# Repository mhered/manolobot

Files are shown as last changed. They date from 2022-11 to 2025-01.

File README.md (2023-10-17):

# README - manolobot

This repo contains my notes documenting the build of my own ROS2-based mobile robot with camera and LIDAR.

This project is inspired in the phenomenal series of blog and video tutorials [Articulated Robotics](https://articulatedrobotics.xyz/) by Josh Newans.

* [Part 1](./Part-1-Getting-ready-ROS2-Aug22-Jan23.md): Notes on Articulated Robotics - Getting ready for ROS series 
* [Part 2](./Part-2-Mobile-Robot-project.md): Notes on Articulated Robotics - Making a Mobile Robot series
* [Part 3](Part-3-manolobot-Nov22.md): Notes on building **manolobot** my own ROS2-based mobile robot with camera and LIDAR
* [Part 4](Part-4-Simulation-Jan23.md): Notes on simulating the robot **manolobot_uno**
* [Part 5](Part-5-Teleoperation-Feb23.md): Notes on teleoperation for **manolobot_uno**

Go straight for the [Quick Start Guide](Quick-start-guide.md) to launch the robot and play with it

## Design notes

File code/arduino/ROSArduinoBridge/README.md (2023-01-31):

# Arduino Motor Controller

Note: Originally downloaded from https://github.com/joshnewans/ros_arduino_bridge.git
Removed .git folder to disconnect it from the original repo

This code turns an Arduino into a motor controller!
It provides a simple serial interface to communicate with a high-level computer (e.g. running ROS), and generates the appropriate PWM signals for a motor driver, to drive two motors.

This is a fork of the original code, with some changes, and removal of the ROS nodes (see [this repo](https://github.com/joshnewans/serial_motor_demo) for an alternative). Check out `README-orig.md` for the original README.

As I only have need for a subset of the functionality, I have no idea what does and doesn't work, beyond what is detailed below.
Feedback/improvements are welcome (though no promises on how quickly I'll respond). I currently only use the L298N driver, and the Arduino encoder mode.

TODO
- Finish this README

## Functionality

The main functionality provided is to receive motor speed requests over a serial connection, and provide encoder feedback.
The original code has provisions for other features - e.g. read/write of digital/analog pins, servo control, but I've never used them.

The main commands to know are

- `e` - Motor responds with current encoder counts for each motor
- `r` - Reset encoder values
- `o <PWM1> <PWM2>` - Set the raw PWM speed of each motor (-255 to 255)
- `m <Spd1> <Spd2>` - Set the closed-loop speed of each motor in *counts per loop* (Default loop rate is 30, so `(counts per sec)/30`
- `p <Kp> <Kd> <Ki> <Ko>` - Update the PID parameters

## Gotchas

Some quick things to note

- There is an auto timeout (default 2s) so you need to keep sending commands for it to keep moving
- PID parameter order is PDI (?)
- Motor speed is in counts per loop
- Default baud rate 57600
- Needs carriage return (CR)
- Make sure serial is enabled (user in dialout group)
- Check out the original readme for more

## TODO (maybe)
- Document PID tuning
- Make the speed input counts per second
- Add/test more driver boards
- Add/test other functionality

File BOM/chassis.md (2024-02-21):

# Chassis

* 290 x 190 x 124 mm Keeeper Hubert + Hilda plastic storage box with tray:  [Amazon](https://www.amazon.de/keeeper-Hubert-Hilda-Storage-Transparent/dp/B092JKYLW5?ref_=ast_sto_dp)
* Caster ball [Amazon](https://www.amazon.es/dp/B09MLVQWL7?_encoding=UTF8&psc=1&ref_=cm_sw_r_cp_ud_dp_PQB2K3KK5H9V853M14GN). Ball diameter 0.6" (16mm)

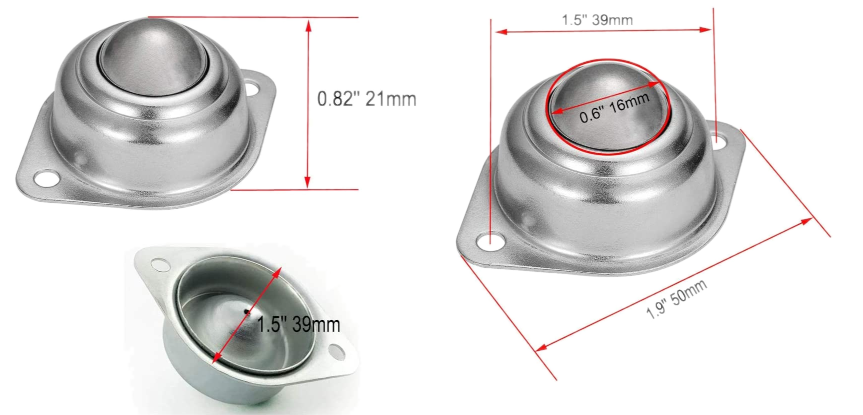
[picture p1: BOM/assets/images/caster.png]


* 2 sets of brass spacers M2.5 2: 20mm and 11mm
* Aluminium profile L shaped 30mm x 17mm x 2mm thickness, cut to 2000mm length
* M3 bolts, washers & nuts

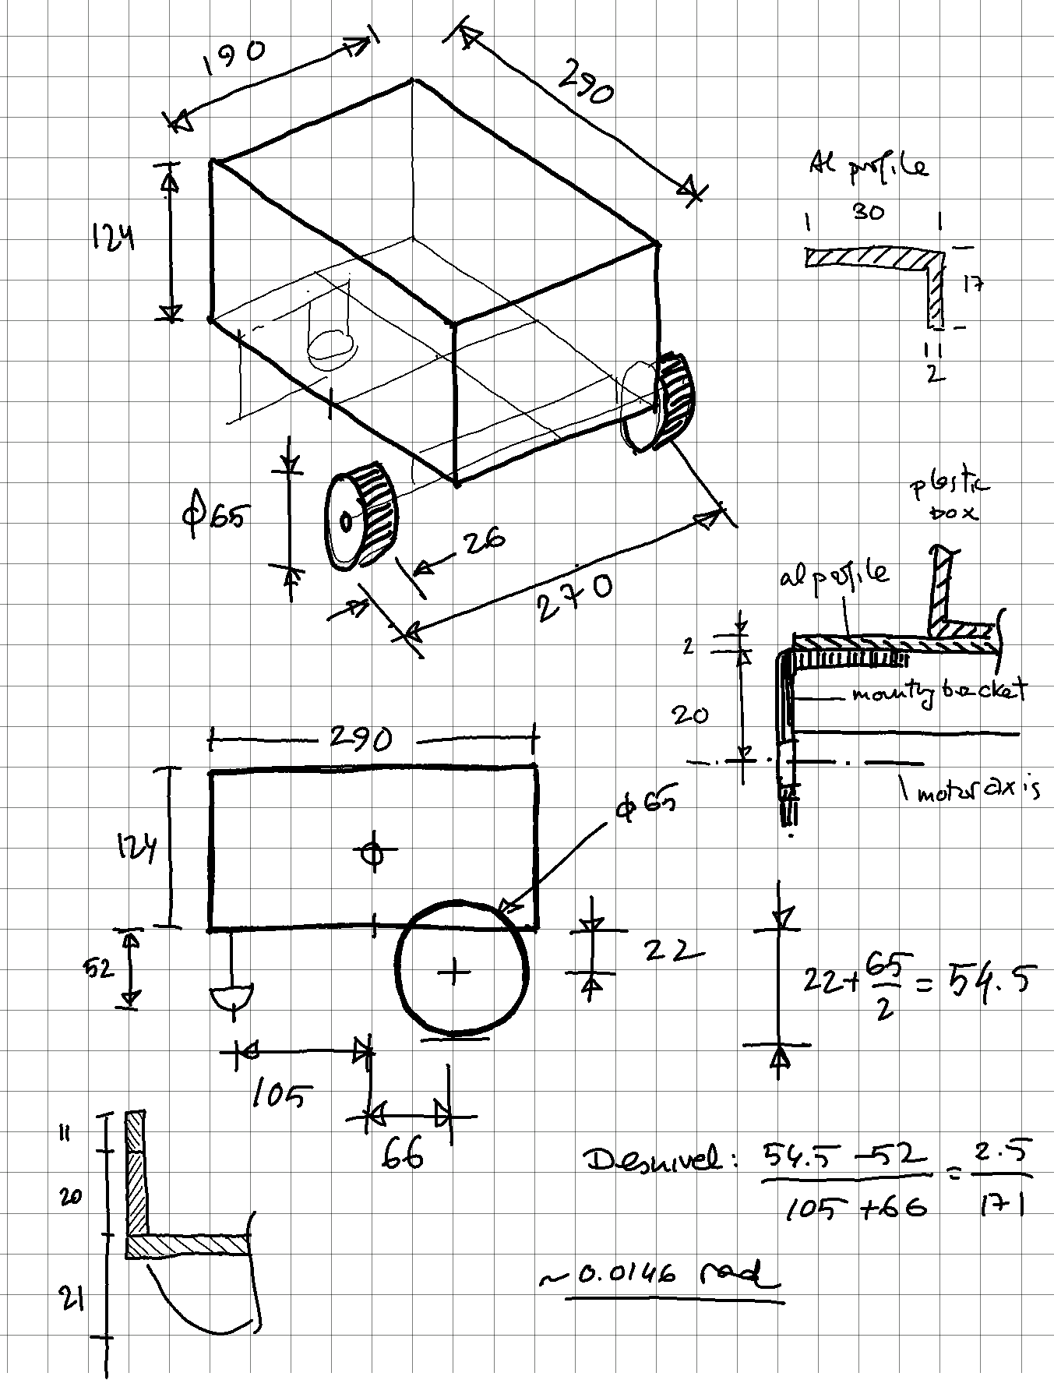
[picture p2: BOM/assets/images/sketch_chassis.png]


## 3D printed parts
### LD06 mount
* [Minipupper Oak-D-Lite & Lidar mount](https://www.thingiverse.com/thing:5374323)
* [LDRobot LD06 360 LiDAR Module & Raspberry PI Mounting Bracket](https://grabcad.com/library/ldrobot-ld06-360-lidar-module-raspberry-pi-mounting-bracket-1)
* [The original LD06 baseplate from my minipupper repo](https://github.com/mhered/minipupper_fun/tree/main/assets/CAD)

### Pi camera mount
* [BEST Micro Apex GO PRO Mount](https://www.thingiverse.com/thing:4890862)
* [Case Raspberry Pi Camera V2 (universal mounting) and GoPro holder adapter](https://www.thingiverse.com/thing:3610624)
* [Pi Camera Mount](https://www.thingiverse.com/thing:3411450)

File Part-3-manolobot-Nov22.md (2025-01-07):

# manolobot

## Bill of Materials

| Qty. | Item | Image | Description | Link | Price |
| ---- | --- | --- | --- | --- | --- |
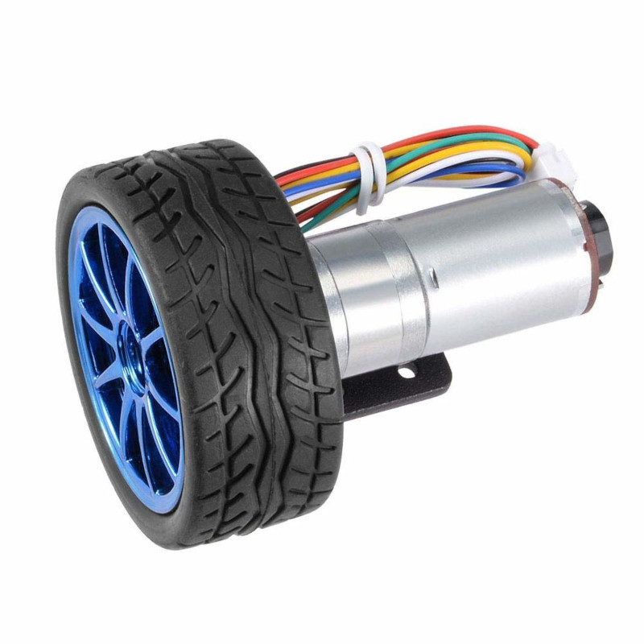
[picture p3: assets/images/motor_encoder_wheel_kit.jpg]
motor_encoder_wheel_kit
| 2 | [12V DC  encoder motor kit](./BOM/motor_kit.md) |  | 12V DC motor JGA25-371 with encoder, 130rpm reductor, 65mm wheel, coupling, mounting bracket | [Amazon](https://www.amazon.es/dp/B07WT22RNK?psc=1&ref=ppx_pop_dt_b_asin_title) | 30,33€ |
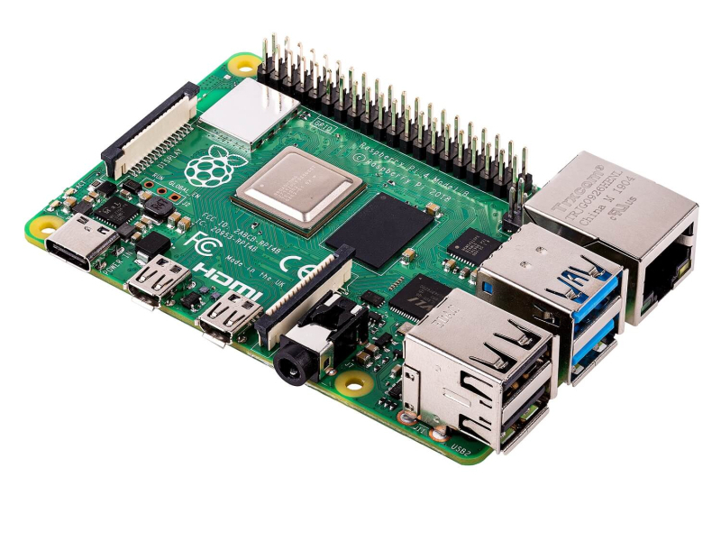
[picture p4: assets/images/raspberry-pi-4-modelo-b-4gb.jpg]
raspberry-pi-4-modelo-b-4gb
| 1 | [Raspberry Pi 4B](./BOM/RPi_4B.md) |  | | [Amazon]() | |
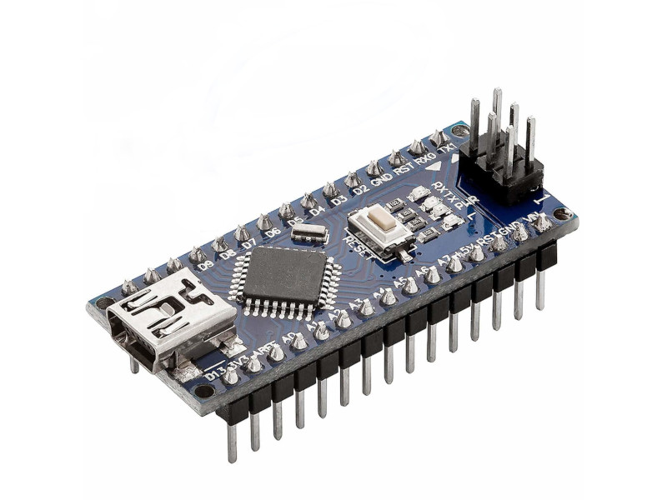
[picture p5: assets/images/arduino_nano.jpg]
arduino_nano
| 1 | [Arduino Nano V3](./BOM/arduino_nano.md) |  | AZDelivery Nano V3.0 with ATmega328 Chip CH340 soldered version with USB cable (Arduino Nano V3 clone) | [Amazon](https://www.amazon.es/gp/product/B01MS7DUEM/ref=ppx_yo_dt_b_asin_title_o00_s00?ie=UTF8&th=1) | 18,99€ |
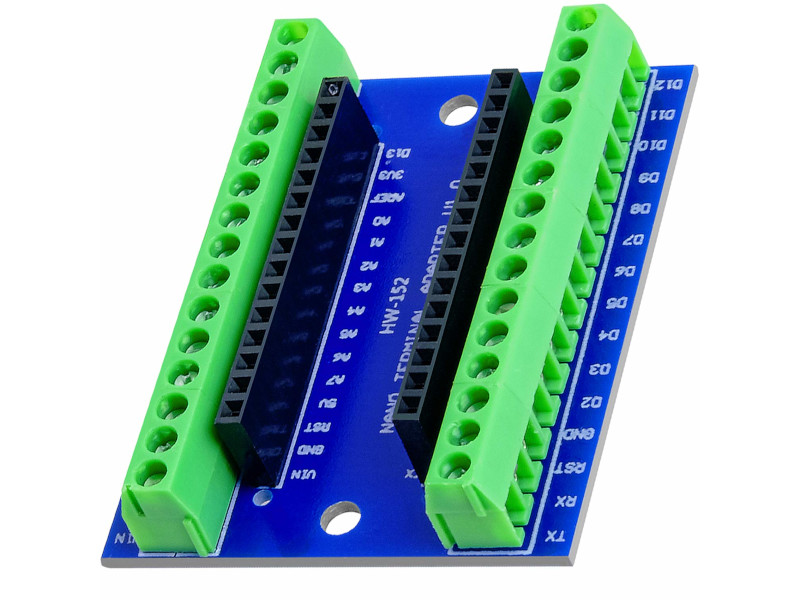
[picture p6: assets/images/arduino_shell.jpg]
arduino_shell
| 1 | Arduino Nano Shell |  | | [Amazon](https://www.amazon.es/gp/product/B08T1ZXS7K/ref=ppx_yo_dt_b_asin_title_o00_s01?ie=UTF8&th=1) | 6,99€ |
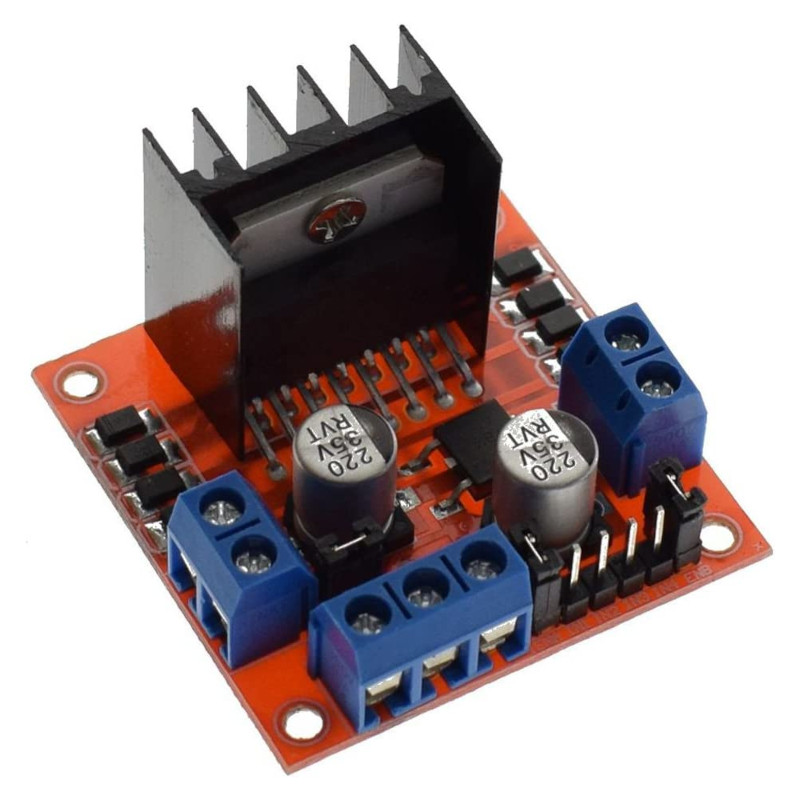
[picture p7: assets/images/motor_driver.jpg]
motor_driver
| 1 | [L298N Motor driver](./BOM/motor_driver.md) |  | | [Amazon](https://www.amazon.es/gp/product/B077NY9RY6/ref=ppx_yo_dt_b_asin_title_o00_s01?ie=UTF8&psc=1) | 9,99€ (2 uds) |
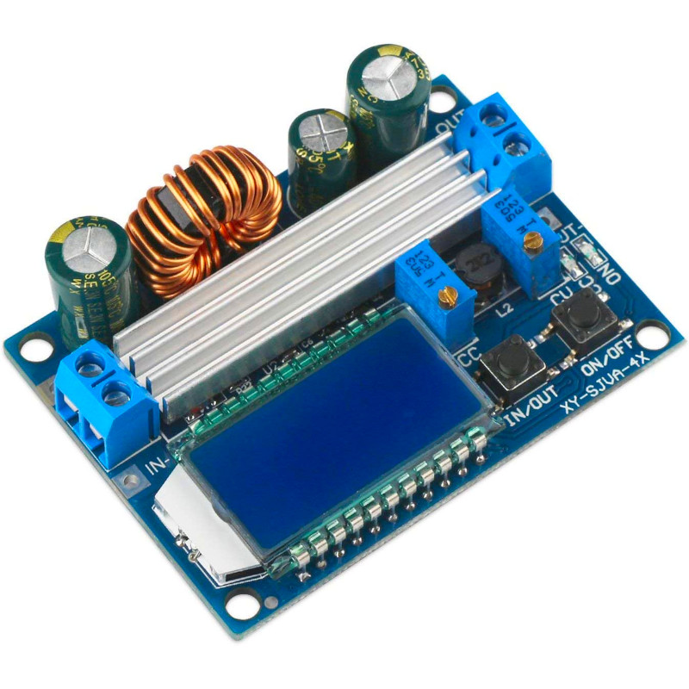
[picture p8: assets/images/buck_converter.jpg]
buck_converter
| 1 | [35W Buck-Boost DC Converter](./BOM/buck_converter.md) |  | ARCELI Buck-Boost Converter with display, DC 5.5-30V 12v to DC 0.5-30V  35W | [Amazon](https://www.amazon.es/gp/product/B07MY399GQ/ref=ppx_yo_dt_b_asin_title_o02_s00?ie=UTF8&psc=1) | 12,99€ |
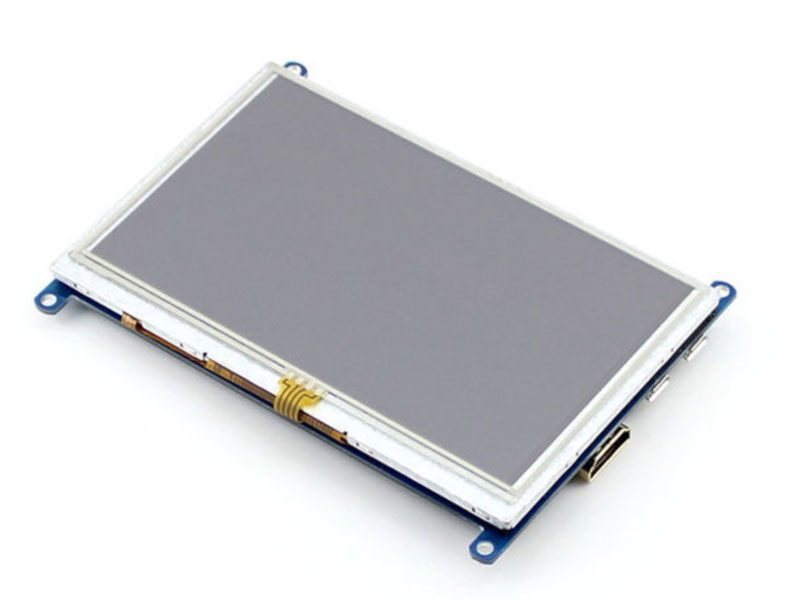
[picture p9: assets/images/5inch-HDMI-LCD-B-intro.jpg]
touchscreen
| 1 | [5" 800x480 Resistive  Touchscreen](./BOM/touchscreen.md) |  | Waveshare 5" HDMI LCD 800x480 Resistive Touchscreen TFT Display  with Case for Raspberry Pi 4 | [Amazon](https://www.amazon.es/dp/B07PLF8V8Y?psc=1&ref=ppx_pop_dt_b_product_details) | 52,99€ |
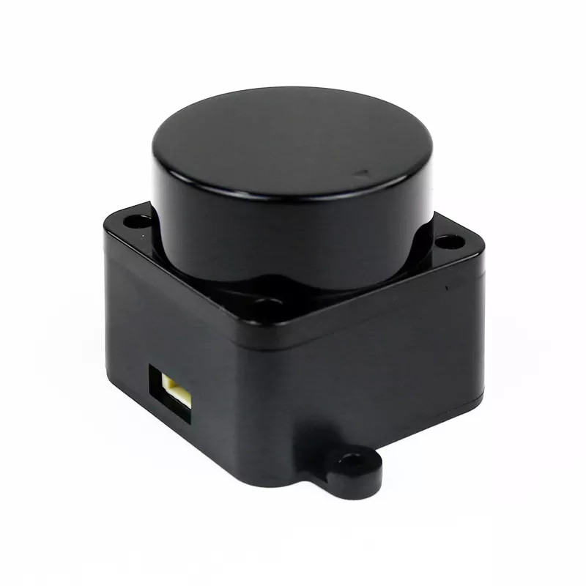
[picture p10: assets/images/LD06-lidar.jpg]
LD06-lidar
| 1 | [DTOF Lidar LD06](./BOM/LD06-lidar.md) |  | LD06 Lidar, came bundled with Minipupper | [Amazon](https://www.amazon.es/innomaker-integrado-omnidireccional-resistencia-LiDAR_LD06/dp/B08GJJX41D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) | 99,99€ |
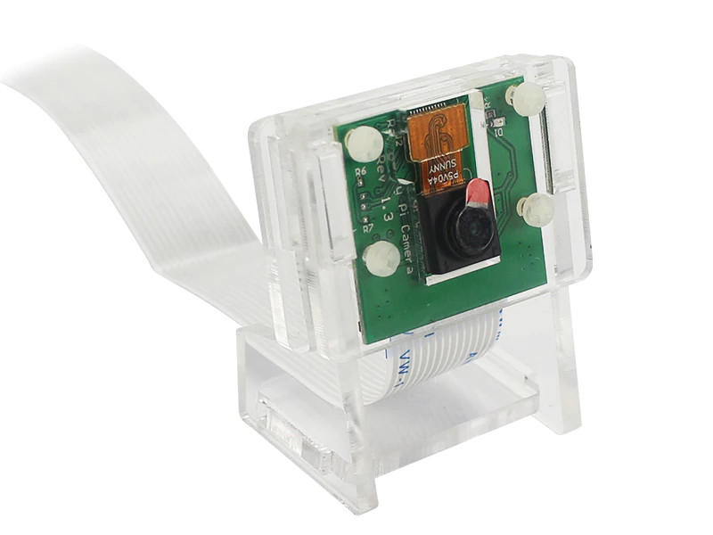
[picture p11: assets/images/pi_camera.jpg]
pi_camera
| 1 | [Pi Camera](./BOM/pi_camera.md) |  | Pi Camera v1.3 with acrilic support | | |
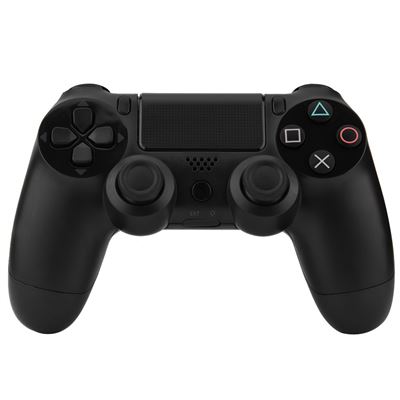
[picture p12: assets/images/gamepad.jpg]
| 1 | [Gamepad](./BOM/gamepad.md) |  | PS4-compatible Bluetooth game controller. Mine came bundled with Minipupper | [Fnac](https://www.fnac.es/mp8198387/Mando-USB-con-cable-Smart-Gamepad-para-PC-PS4/w-4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) | 17,90€ |
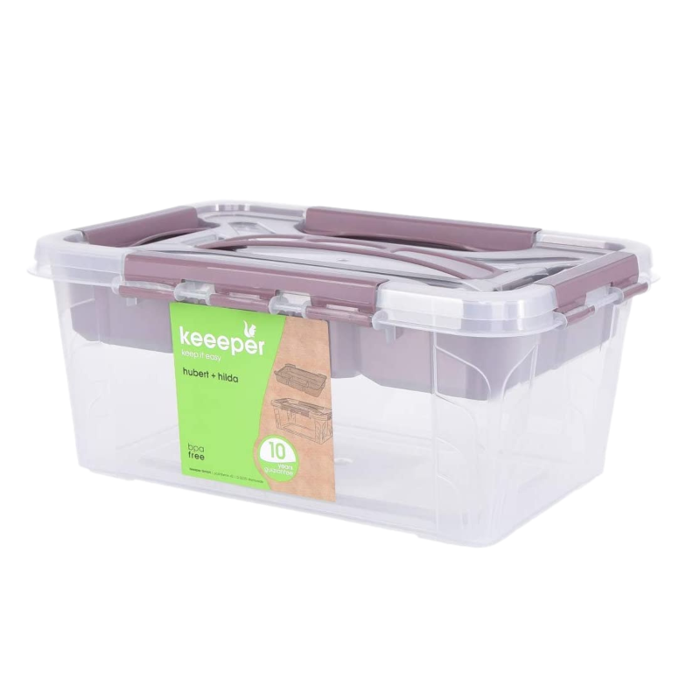
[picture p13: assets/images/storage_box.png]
| 1 | [Chassis](./BOM/chassis.md) |  | Based on a 29 x 19 x 12.4 cm Keeeper Hubert + Hilda plastic storage box with tray, used for the chassis of the robot. I purchased mine in the local Leroy Merlin. | [Amazon](https://www.amazon.de/keeeper-Hubert-Hilda-Storage-Transparent/dp/B092JKYLW5?ref_=ast_sto_dp) | 8,63€ |
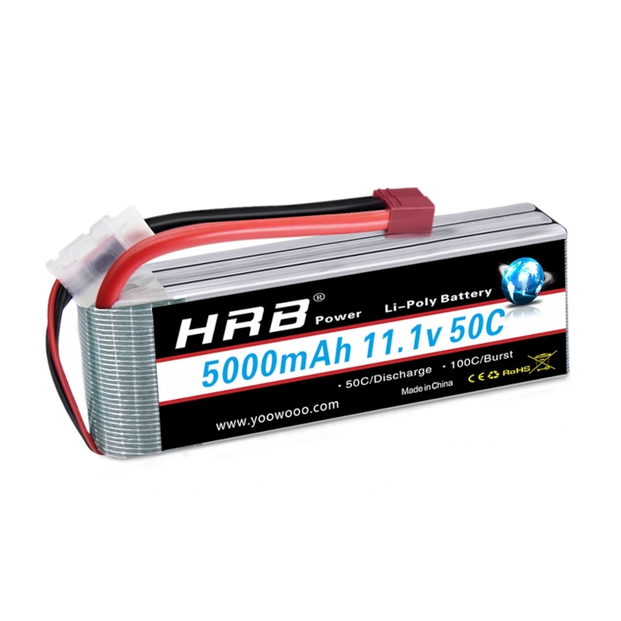
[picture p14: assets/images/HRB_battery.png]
| 1 | [Battery](./BOM/battery.md) |  | HRB Battery RC LiPo 5000mAh 11.1V 3S 50C XT60 Connector with 4 adapter parts. 308 g. | [Amazon](https://www.amazon.es/gp/product/B086JP7PCC/) | 35,99€ |
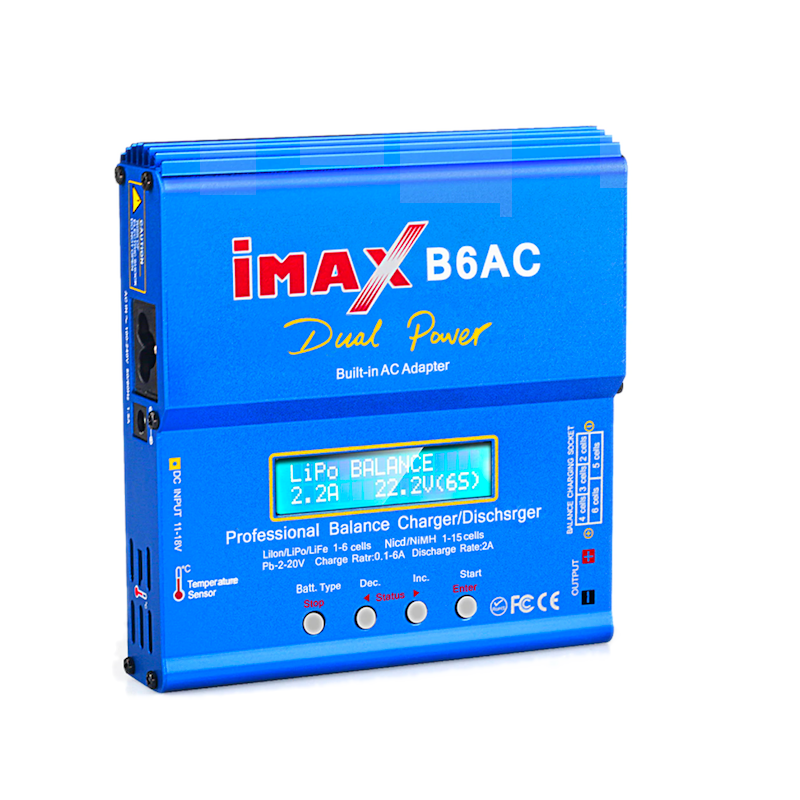
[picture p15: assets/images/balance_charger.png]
| 1 | Balance charger |  | WANGCL IMAX B6AC Lipo Battery charger B6 80W Digital LCD Lipo Cargador  11-18V con adaptador para plomo ácido NI-CD/NI-MH 1-6S LI-PO | [Amazon](https://www.amazon.es/gp/product/B0B3GM8KX9/) | 42,99€ |
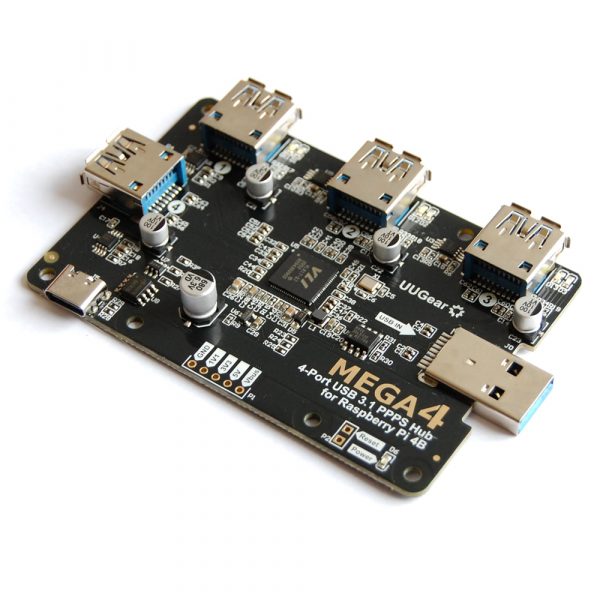
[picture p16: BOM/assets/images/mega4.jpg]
| 1 | [Mega4 USB Hub](./BOM/mega4.md) |  | UUGEAR MEGA4: 4-Port USB 3.1 PPPS Hub for Raspberry Pi 4B | [The Pi Hut](https://thepihut.com/products/mega4-4-port-usb-3-1-ppps-hub-for-raspberry-pi-4) | £29,00 |

## First prototype (20/11/22)

- 12V from bench power source
- A split takes the 12V to the buck converter and the motor driver.
- Buck converter takes 12V at IN+ /IN- and yields 5V at OUT+/OUT- to power the RPi
- RPi takes 5V at pin 4 (5V)/ pin 6(GND) - [How do I power my Raspberry Pi](https://robocraze.com/blogs/post/how-do-i-power-my-raspberry-pi)
- Arduino Nano powered from RPi via USB
- Motor Driver is powered by 12V at 12V/GND pins. 5V jumper is installed, 5V terminal not connected - Could I use this to power the RPi?
- OUT1/OUT2 are connected to the Red/White of the motor. The remaining 4 cables of the encoder are disconnected.
- Connecting the IN1 / IN2 to 5V (e.g. to the 5V pin of the Arduino Nano, cfr. [the Nano pinout in this tutorial](https://diyi0t.com/arduino-nano-tutorial/)) makes the Motor rotate CV / CCV  

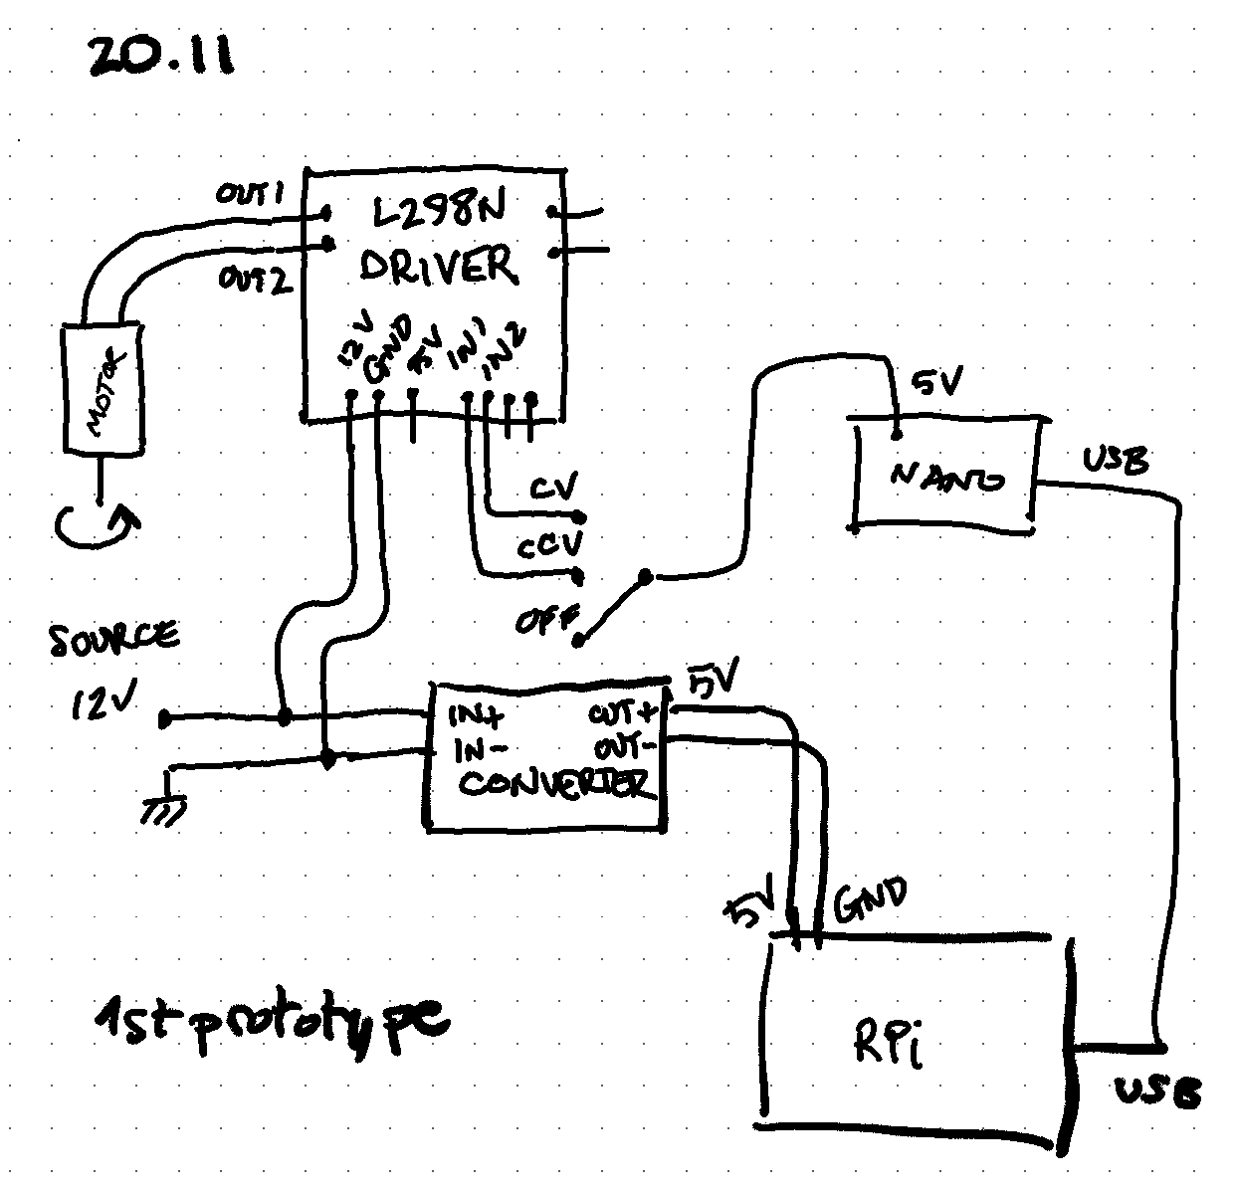
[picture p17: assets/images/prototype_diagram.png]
prototype_diagram


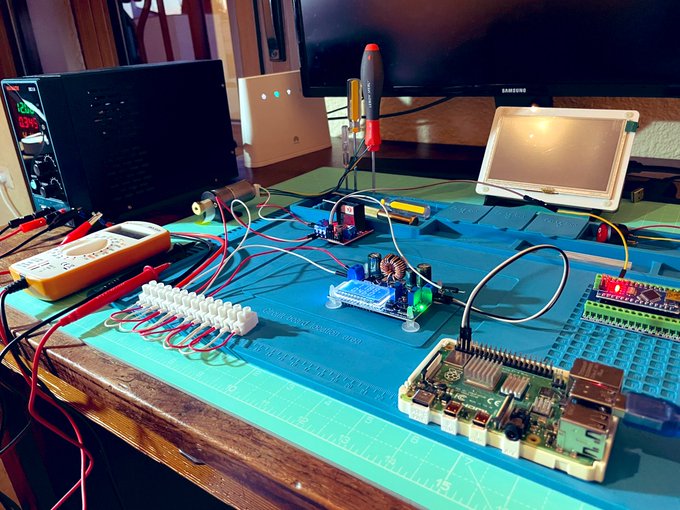
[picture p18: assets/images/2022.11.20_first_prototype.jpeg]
first_prototype


### Shutting down

Before switching off the power supply, SSH into the RPi to shut it down:

```bash
(RPi) $ sudo shutdown -h now
```

Note: Powering the adafruit USB hub https://forums.adafruit.com/viewtopic.php?p=930206&hilit=external+power+usb+hub#p930206

## Prototype status (4/12/22)

- installed fuse and switch
- replaced split with AWG22 cable
- installed second motor
- connected Pi camera, LD06 lidar and LCD screen
- made a USB-C pigtail to connect RPi (powering from pins cannot run accesories)
- ordered spacers, USB-C pigtails, a flat HDMI cable and a USB hub

## Prototype status (28/12/22)

* installed flat HDMI cable, USB-C pigtail
* discarded USB hub (not needed)

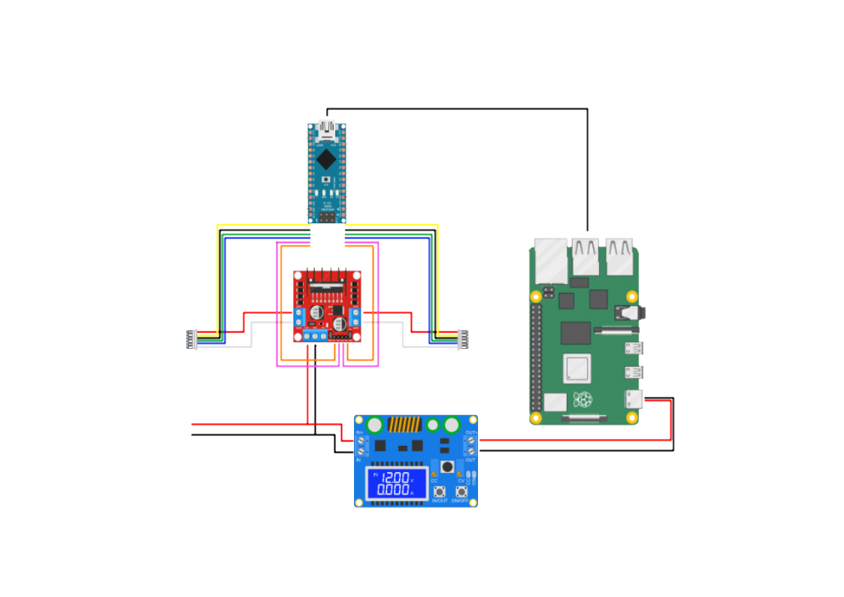
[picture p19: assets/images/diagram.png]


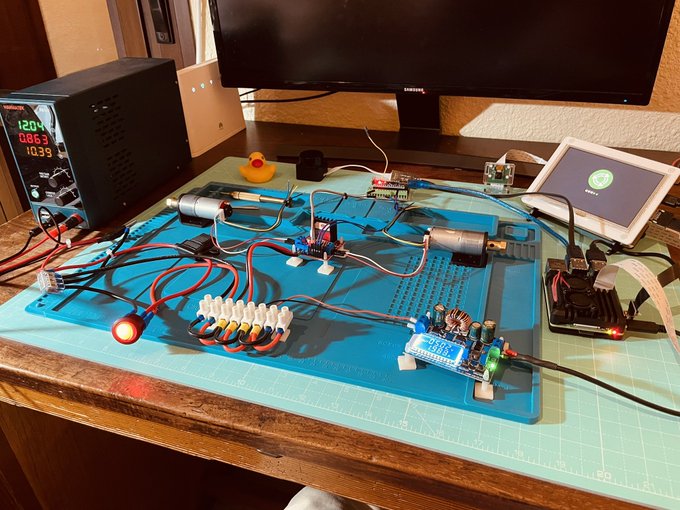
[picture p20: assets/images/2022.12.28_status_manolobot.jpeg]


## Controlling the motors with a joystick (4/1/23)

Code: [./code/arduino/motor_joystick/motor_joystick.ino](./code/arduino/motor_joystick/motor_joystick.ino) 

The script was originally inspired on [this example code for the joystick](https://www.luisllamas.es/arduino-joystick/) and [this script for controlling motors](https://lastminuteengineers.com/l298n-dc-stepper-driver-arduino-tutorial/), and later refined with [this implementation](https://howtomechatronics.com/tutorials/arduino/arduino-dc-motor-control-tutorial-l298n-pwm-h-bridge/) (using [Arduino's map() function](https://www.arduino.cc/reference/en/language/functions/math/map/) ) and [this discussion on translating joystick positions to motor speeds](https://coderdojoathenry.org/2019/02/24/hackers-how-to-control-a-robots-wheel-motors-based-on-joystick-movements/).

Notes:

* For motors A and B connect only motor voltage (WHITE, RED) to the motor driver L298N, keeping encoder disconnected (BLUE,GREEN, BLACK,YELLOW)
* In the motor driver L298N, remove the brakers in ENA and ENB 
* Connect as per following table and diagram:

| Description | Component pin | Arduino pin |
| --- | ---- | ---- |
| Motor A speed (analog) | ENA  | D9 |
| Motor A direction | IN1 | D8 |
| Motor A direction | IN2 | D7 |
| Motor B speed (analog) | ENB | D3 |
| Motor B direction | IN3 | D5 |
| Motor B direction | IN4 | D4 |
| Joystick: command rotation (analog) | VRX | A0 |
| Joystick: command forward / backward motion (analog) | VRY | A1 |

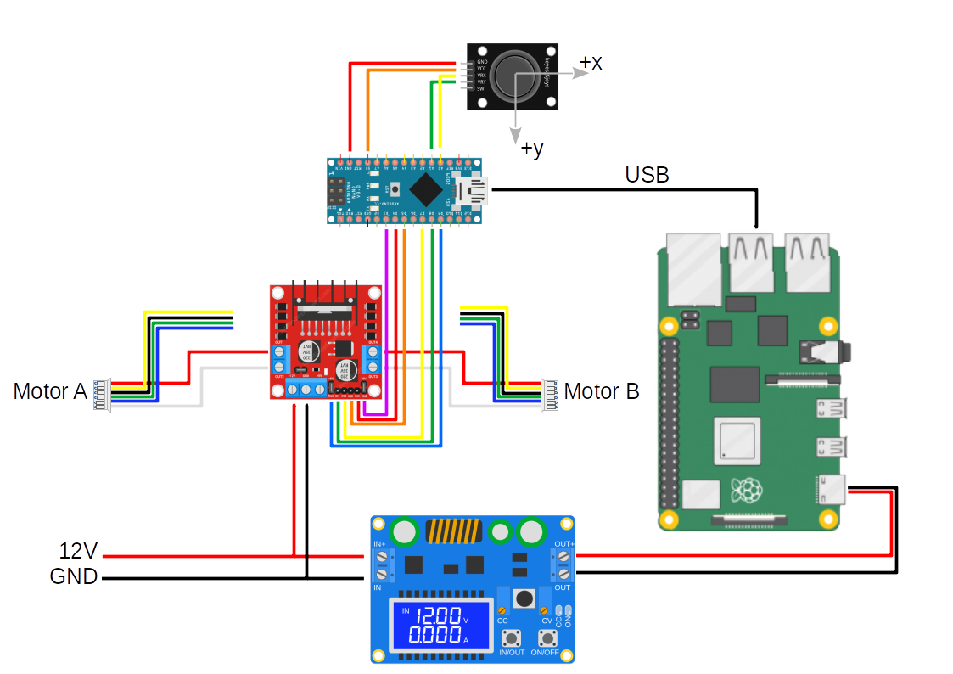
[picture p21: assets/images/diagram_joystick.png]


* Analog output of VRX, VRY is in the range 0 - 1023. 
* Analog input of ENA and ENB in the range 0-255. 
* To change direction of rotation of Motor A reverse input to IN1 - IN2  from HIGH - LOW to LOW - HIGH
* Idem for Motor B, IN3, IN4

The script allows to control the motors with the joystick. Moving the stick in the Y direction turns both wheels forward / backward. Moving the stick in X direction moves the wheels in opposite directions to make the robot turn. The script also prints output through serial. 

## `miniterm` to monitor serial in the Arduino from the laptop (and through the RPi)

1. install `miniterm` in PC and RPi

```bash
$ sudo apt install python3-serial
```

2. add the user to the dialout group:

```bash
$ sudo adduser mhered dialout
```

3. usage:

```bash
$ miniterm

--- Available ports:
---  1: /dev/ttyAMA0         'ttyAMA0'
---  2: /dev/ttyUSB0         'USB2.0-Ser!'
--- Enter port index or full name: 2
--- Miniterm on /dev/ttyUSB0  9600,8,N,1 ---
--- Quit: Ctrl+] | Menu: Ctrl+T | Help: Ctrl+T followed by Ctrl+H ---
(X, Y): (508, 517) | motorA: 0% | motorB: 1%
(X, Y): (510, 517) | motorA: 0% | motorB: 1%
(X, Y): (510, 517) | motorA: 0% | motorB: 1%
(X, Y): (510, 516) | motorA: 0% | motorB: 1%
(X, Y): (510, 22) | motorA: -96% | motorB: -95%
(X, Y): (493, 0) | motorA: -100% | motorB: -96%
(X, Y): (510, 517) | motorA: 0% | motorB: 1%
(X, Y): (510, 1023) | motorA: 99% | motorB: 100%
(X, Y): (510, 1022) | motorA: 99% | motorB: 100%
(X, Y): (1023, 1023) | motorA: 100% | motorB: 0%
(X, Y): (1023, 850) | motorA: 100% | motorB: -34%
(X, Y): (1023, 517) | motorA: 100% | motorB: -99%
(X, Y): (661, 517) | motorA: 29% | motorB: -28%
(X, Y): (0, 517) | motorA: -99% | motorB: 100%
(X, Y): (0, 517) | motorA: -99% | motorB: 100%
...
```

Note: to stop `miniterm` with a Spanish keyboard press  `Ctrl + Alt Gr + ]` 

## VS Code Remote and Arduino extensions

Check out this video on how to write and upload to arduino from the laptop and through the RPi: https://www.youtube.com/watch?v=2BJ-iJF04VA

Highlights of the installation:

* Copy & Paste **only** the path of the folder where the `arduino` executable is, e.g. in the case below paste only `/home/mhered/Applications/arduino-1.8.19/`:

`````bash
$ ls -l `which arduino`
lrwxrwxrwx 1 root root 48 Sep  9 02:02 /usr/local/bin/arduino -> /home/mhered/Applications/arduino-1.8.19/arduino
`````

* No need to select a programmer, see [here](https://support.arduino.cc/hc/en-us/articles/6125080065820-Select-programmer-in-Arduino-IDE)
* Edit `.vscode/arduino.json` to add `"output":"build"` to avoid the message that it cannot use precompiled files

Highlights of the usage:

* To launch **Remote SSH** click in the green square in the bottom left corner of VS Code, select **Connect to Host** and select the host, then enter the password
* Every new session: Open the Command panel with  `Ctrl + Shift + P` then start typing "Select" for **Arduino: Select Sketch**. The file `.vscode/arduino.json` stores the selection of `port`, `sketch`, `board`, `configuration`, `output` otherwise select manually in the lower blue bar.
* To compile: command **Arduino: Verify**. Monitor progress on the OUTPUT / Arduino window. Wait for it to finish before uploading.
* To flash: command **Arduino: Upload**. Wait for compile to complete before uploading. Does not work if `miniterm` is running.
* To monitor serial: use `miniterm` in a new Terminal
* To add libraries: command **Arduino: Library Manager**

## Chassis (7/1/23)

* First test on the chassis

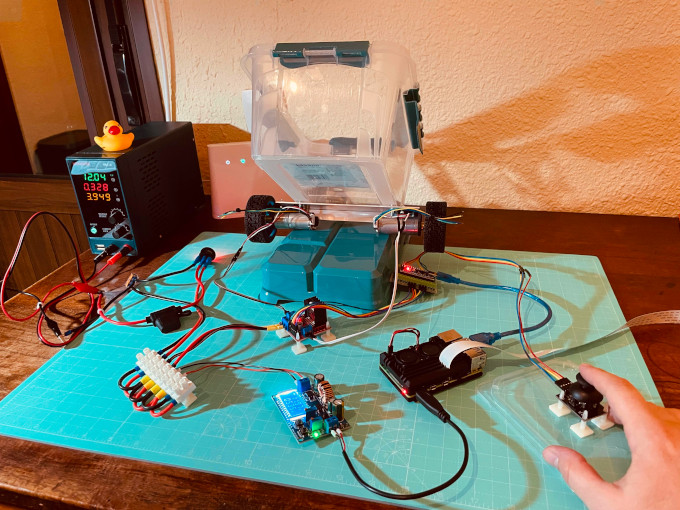
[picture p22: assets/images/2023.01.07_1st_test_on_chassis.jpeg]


* All aboard! - including the rubber duckie

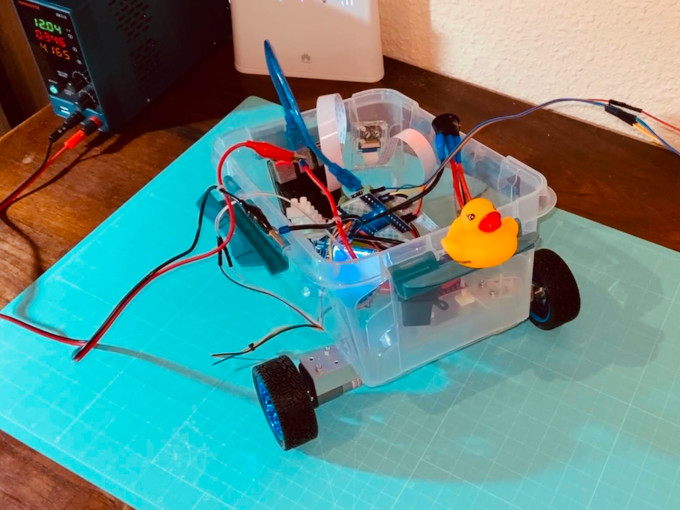
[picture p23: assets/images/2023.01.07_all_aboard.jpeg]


## Details (12/1/23)

* Adding details: casters, grommets, a switch...

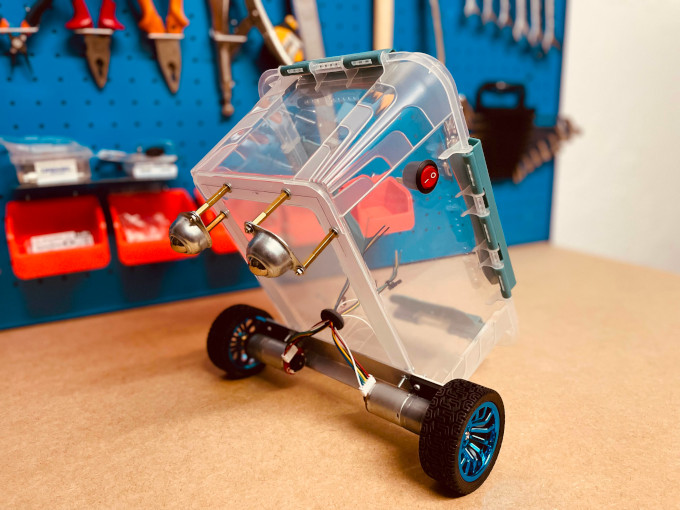
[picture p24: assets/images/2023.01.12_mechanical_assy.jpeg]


* All the electronics back in



## Order in the house (17/1/23)

* Some order inside the chassis:



## Selfie  (21/1/23)

* A selfie to celebrate that the camera onboard the `manolobot_uno ` is broadcasting!



## Prototype status (29/01/23)

* Screen, safe reset/shutdown button and 3D printed camera support







## Running motors from the PC (31.01.23)

1. Clone `ROSArduinoBridge` from https://github.com/joshnewans/ros_arduino_bridge.git to `./code/arduino/` - removed the `.git` folder to disconnect it from original repo
2. Upload software to the Arduino
3. Rewire Arduino:

| Description | From | To |
| --- | --- | --- |
| Motor A (Left) , power + (can be reversed with White to move motor forward and reverse) | Motor A (Left) , Red | L298, OUT1 |
| Motor A (Left), power - (can be reversed with Red to move motor forward and reverse) | Motor A (Left) , White | L298, OUT2 |
| Motor B (Right), power + (can be reversed with White to move motor forward and reverse) | Motor B (Right), Red | L298, OUT4 |
| Motor B (Right), power - (can be reversed with Red to move motor forward and reverse) | Motor B (Right), White | L298, OUT3 |
| Motor A (Left) direction | L298, IN1 | Arduino, D10 |
| Motor A (Left) direction | L298, IN2 | Arduino, D6 |
| Motor B (Right) direction | L298, IN3 | Arduino, D9 |
| Motor B (Right) direction | L298, IN4 | Arduino, D5 |



4. Run `miniterm` to test it (`-e` for interactive and specify the baud rate or it won't work at 9600):

```bash
(RPi):$ $ miniterm -e /dev/ttyUSB0 57600
--- Miniterm on /dev/ttyUSB0  57600,8,N,1 ---
--- Quit: Ctrl+] | Menu: Ctrl+T | Help: Ctrl+T followed by Ctrl+H ---
o 150 150
OK
o -200 200
OK
--- exit ---
```

## With encoders

Wiring:



| Description | From | To |
| --- | --- | --- |
| Motor A (Left) , power + (can be reversed with Red to move motor forward and reverse) | Motor A (Left) , Red | L298, OUT1 |
| Motor A (Left), Encoder power - (Voltage range 3.3-5V. Positive and negative can not be connected incorrectly) | Motor A (Left) , Black | Arduino, GND |
| Motor A (Left), Encoder A phase signal feedback (11 signals per turn of the motor) | Motor A (Left) , Yellow | Arduino, D3 |
| Motor A (Left), Encoder B phase signal feedback (11 signals per turn of the motor) | Motor A (Left) , Green | Arduino, D2 |
| Motor A (Left), Encoder power supply + (Voltage range 3.3-5V. Positive and negative can not be connected incorrectly) | Motor A (Left) , Blue | Arduino, 5V |
| Motor A (Left), power - (can be reversed with Red to move motor forward and reverse) | Motor A (Left) , White | L298, OUT2 |
| Motor B (Right), power + (can be reversed with Red to move motor forward and reverse) | Motor B (Right), Red | L298, OUT4 |
| Motor B (Right), Encoder power - (Voltage range 3.3-5V. Positive and negative can not be connected incorrectly) | Motor B (Right), Black | Arduino, GND |
| Motor B (Right), Encoder A phase signal feedback (11 signals per turn of the motor) | Motor B (Right), Yellow | Arduino, A4 |
| Motor B (Right), Encoder B phase signal feedback (11 signals per turn of the motor) | Motor B (Right), Green | Arduino, A5 |
| Motor B (Right), Encoder power supply + (Voltage range 3.3-5V. Positive and negative can not be connected incorrectly) | Motor B (Right), Blue | Arduino, 5V |
| Motor B (Right), power - (can be reversed with Red to move motor forward and reverse)e | Motor B (Right), White | L298, OUT3 |
| Motor A (Left) direction | L298, IN1, Green | Arduino, D10 |
| Motor A (Left) direction | L298, IN2, Yellow | Arduino, D6 |
| Motor B (Right) direction | L298, IN3, Orange | Arduino, D9 |
| Motor B (Right) direction | L298, IN4, Red | Arduino, D5 |

## Calibration

See https://www.youtube.com/watch?v=-PCuDnpgiew

`encoder_cpr` empirically estimated as 1975 encoder counts / revolution

`loop_rate` (or `PID_RATE`) is set to 30 Hz (PID loops/s)

To set a wheel speed of R rev/s we send to the closed loop a command in counts per PID loop so: 

(R rev/s) * (1975 counts/rev) /(30 PID loops/s) = R*1975/30 counts/PID loop = 66 R counts/PID loop

i.e. to rotate both wheels forward at 1 rev/s: `m 66 66`

to rotate both wheels backwards at 2 rev/s: `m -132 -132`

etc

## To do

- [x] connect motors 
- [x] install and test basic motor software
- [x] configure and test camera
- [x] configure and test lidar
- [x] purchase and install battery
- [x] soft powerdown button
- [x] USB hub
- [x] solve issues with screen
- [x] 3D printed parts
- [x] connect and test encoders
- [x] command motor through ROS 
- [x] teleoperation with gamepad
- [ ] improve layout of components inside chassis
- [ ] configure face in screen

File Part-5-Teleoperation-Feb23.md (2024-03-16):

# Teleoperation

Teleoperation is about sending command signals to the robot, and receiving sensor feedback from the robot.

Roadmap:

- Demo GUI ROS node
- `teleop_twist_keyboard` with `ros2_control`
- teleop with a gamepad
- teleop with a phone

## Demo GUI ROS node

1. In the RPi clone the repo and symlink to src, build and source:

```bash
(RPi): $ cd ~/git/ && git clone https://github.com/joshnewans/serial_motor_demo.git
(RPi): $ ln -s ~/git/serial_motor_demo/ ~/dev_ws/src/
(RPi): $ cd ~/dev_ws/
(RPi): $ colcon build --symlink-install
(RPi): $ source install/setup.bash
```

2. Run the driver node in the RPi:

```bash
(RPI):$ ros2 run serial_motor_demo driver --ros-args -p serial_port:=/dev/ttyUSB0 -p baud_rate:=57600 -p loop_rate:=30 -p encoder_cpr:=1975
Connecting to port /dev/ttyUSB0 at 57600.
Connected to Serial<id=0xffff80b8ec40, open=True>(port='/dev/ttyUSB0', baudrate=57600, bytesize=8, parity='N', stopbits=1, timeout=1.0, xonxoff=False, rtscts=False, dsrdtr=False)
Error: Serial timeout on command: e

```

3. Repeat the process in the PC and run the GUI:

```bash
(PC): $ cd ~/git/ && git clone https://github.com/joshnewans/serial_motor_demo.git
(PC): $ ln -s ~/git/serial_motor_demo/ ~/dev_ws/src/
(PC): $ colcon build --symlink-install
(PC): $ cd ~/dev_ws/
(PC): $ source install/setup.bash

(PC):$ ros2 run serial_motor_demo gui
```



## Teleop with the keyboard (`teleop_twist_keyboard` and `ros2_control`)

cfr: https://articulatedrobotics.xyz/mobile-robot-12-ros2-control/

cfr: https://control.ros.org/master/index.html

Using ROS topics is not fast enough

`ros2_control` is faster (loads libraries) and allows writing modular reusable code



### Controller manager

**Controller manager** connects hardware drivers with control algorithms using plugins

2 ways to run it:

* normally you use the one provided `controller_manager/ros2_control_node`
* you may want to write your own node of class `controller_manager::ControllerManager`

Provide info about the hardware interfaces via the URDF file and the controllers via a YAML parameters file

Interacting with the controller manager:

* via ROS services
* via `ros2_control` CLI tool that simplifies the calls to these services
* via specialized nodes and scripts

### Hardware interfaces 

**Hardware interfaces or components** are pieces of software that speak to the hardware and expose it in the standard of `ros2_control`. They represent the hardware through **Command interfaces** (read/write, things we can control in the robot, e.g. motor velocity) and **State interfaces** (read only, things we can only monitor, e.g. wheel position and velocity, battery level, temperature, etc)

A robot may have multiple hardware components. The **controller manager** uses the **resource manager** to gather all the hardware interfaces and exposes them together so the controller manager sees a long list of command and state interfaces. We include `ros2_control` tags in the URDF to list the hardware interfaces (plugins) the resource manager must load.

### Controllers

The way we interact with `ros2_control` listen for input e.g. gamepad or navigation path planner

They listen for some topic, calculate proper actuations and send command inputs to the hardware interfaces through controller manager and resource manager

Controllers are designed for specific robot applications, and are hardware independent. Many are provided in `ros2_controller` package. E.g. the `diff_drive_controller/DiffDriveController`

We set up the controllers through a YAML file that sets parameters

We can have several controllers provided they are not trying to command the same interfaces, but they can share state interfaces (read only)

Controllers do not need to actually control anything, can be used e.g. just to read a state interface and publish it to a ROS topic

### In practice (with gazebo)

1. Install packages:

```bash
(PC):$ sudo apt install ros-foxy-ros2-control ros-foxy-ros2-controllers ros-foxy-gazebo-ros2-control
```

2. update URDF file `./manolobot_uno/description/robot.urdf.xacro` to call `ros2_control.xacro` instead of `gazebo_control.xacro`
3. Create [`./manolobot_uno/description/ros2_control.xacro`](./manolobot_uno/description/ros2_control.xacro) and YAML parameter file `./manolobot_uno/config/my_controllers.yaml`
4. build and source
5. run with:

```bash
(PC):$ ros2 launch manolobot_uno launch_sim.launch.py world:=./src/manolobot_uno/worlds/cones.world
```

6. Check hardware interfaces are working with:

```bash
(PC):$ ros2 control list_hardware_interfaces
command interfaces
	left_wheel_joint/velocity [unclaimed]
	right_wheel_joint/velocity [unclaimed]
state interfaces
	 left_wheel_joint/position
	 left_wheel_joint/velocity
	 right_wheel_joint/position
	 right_wheel_joint/velocity
```

7. start controllers with the `spawner.py` script which will later on work nicely for a launch file

```bash
(PC):$ ros2 run controller_manager spawner.py diff_cont
```

8. To run `teleop_twist_keyboard` we need to remap `/cmd_vel` to  `/diff_cont/cmd_vel_unstamped` which is what the controller expects:

```bash
(PC):$ ros2 run teleop_twist_keyboard teleop_twist_keyboard --ros-args -r /cmd_vel:=/diff_cont/cmd_vel_unstamped
```

### In practice (fixing details)

cfr: https://articulatedrobotics.xyz/mobile-robot-12a-ros2-control-extra/

#### Increase gazebo clock rate

Robot movement is choppy because clock rate in Gazebo is too slow (10Hz). Increased to 400Hz because why not.

**Note:** After implementing the fix to increase gazebo clock rate, I get the following error message when running gazebo - even though it otherwise  seems to be working fine:

```
...
[gzserver-2] Error [parser.cc:403] Error parsing XML in file [/home/mhered/dev_ws/install/manolobot_uno/share/manolobot_uno/config/gazebo_params.yaml]: Error document empty.
...
```

If appears it is trying to interpret the `gazebo_params.yaml` file as XML and failing.

#### Reduce wheel drift

Replace wheel collision model for spheres

#### Add parameter to toggle between `gazebo_control` and `ros2_control`

Because `ros2_control` shows misbehavior at higher speeds (?)

- [x] To Do: add toggle at runtime, i.e. `$ ros2 launch my_package launch_sim.launch.py use_ros2_control:=false`

### In practice (in the actual robot)

cfr: https://articulatedrobotics.xyz/mobile-robot-13-ros2-control-real/

We want to link the command velocity (`Twist` or `TwistStamped` messages from a gamepad or Nav2 or whatever) with the actual motors in the robot.

In our case:

* we use the `diff_drive_controller` controller plugin to convert command velocities into required wheel velocities. 
* we need to write a hardware interface plugin or clone `diffdrive_arduino` by Josh Newans - this converts required wheel velocities into motor hardware commands
* The controller manager (`ros2_control_node`) links the two plugins.
* Joint State Broadcaster reads wheel encoder positions and publishes to `/joint_states`so the Robot State Publisher can publish its TFs.

1. Install the hardware interface plugin (clone and symlink the two repos, install `ros2-control`, and build):

```bash
(RPi):$ cd ~/git
(RPi):$ git clone https://github.com/joshnewans/diffdrive_arduino
(RPi):$ ln -s ~/git/diffdrive_arduino/ ~/dev_ws/src/
(RPi):$ git clone https://github.com/joshnewans/serial
(RPi):$ ln -s ~/git/serial/ ~/dev_ws/src
(RPi):$ sudo apt install ros-foxy-ros2-control ros-foxy-ros2-controllers
(RPi):$ cd ~/dev_ws
(RPi):$ colcon build --symlink-install
```

2. Configure it: first, update the URDF file `ros2_control.xacro` so it loads the hardware interface plugin `diffdrive_arduino/DiffDriveArduino` and define all the parameters. Next, create `launch_robot.launch.py` and replace the call to gazebo controller for the `controller_manager` node passing as parameters the URDF in `robot_description` and with the controller plugins in `my_controllers.yaml`. Then,  remove the use of sim time in `launch_robot.launch.py`, and `my_controller_params.yaml` . Finally, delay the launch of `controller_manager`, `diff_drive` and `joint_broad`.

## Teleop with a gamepad

See details in [./BOM/gamepad.md](./BOM/gamepad.md)

It is possible to connect a gamepad to the PC and fwd the commands to the robot (easier to setup for both simulated and real robot) or directly connect it to the robot (lower latency and better perfo). Can also set up both.

A `joy_node` node talks to the joystick driver and publishes `/joy` messages with the commands

Other nodes subscribe and take actions. In particular `teleop_twist_joy` calculates and publishes `Twist` messages with velocities to `/cmd_vel` topic.

##  Teleop with a phone

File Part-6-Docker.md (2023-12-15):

# Docker for robotics

## Part 1: Docker for robotics

See Articulated Robotics video: https://www.youtube.com/watch?v=XcJzOYe3E6M

### What is docker?

Vocabulary: 

* Run an image to create a container

* Start and stop containers 

* Destroy and Run again to reset 

### 6 reasons to use docker in robotics

1. Running incompatible software/OS/hardware
2. Standardized build/test environment
3. Standardized development environment
4. Simplified deployment
5. Infrastructure as code
6. Cloud development

### Docker demo

Currently using ROS2 Foxy in Ubuntu 20.04:

```bash
$ lsb_release -a
No LSB modules are available.
Distributor ID:	Ubuntu
Description:	Ubuntu 20.04.6 LTS
Release:	20.04
Codename:	focal
$ ls /opt/ros
foxy  noetic
```

Pull a docker image of ROS humble:

```bash
$ docker image pull ros:humble
...
Status: Downloaded newer image for ros:humble
docker.io/library/ros:humble
```

```bash
$ docker image ls
REPOSITORY   TAG      IMAGE ID       CREATED      SIZE
ros          humble   a2cfb6110191   4 days ago   752MB
...
```

Run the image (this creates container `f17bdfd41c3e`  and runs as `root`):

```bash
$ docker run -it ros:humble
root@f17bdfd41c3e:/# 
```

Note inside the container we run Ubuntu 22.04 and ROS2 Humble:

```bash
# lsb_release -a
No LSB modules are available.
Distributor ID:	Ubuntu
Description:	Ubuntu 22.04.3 LTS
Release:	22.04
Codename:	jammy
# ls /opt/ros
humble
```

We can list containers running:

```bash
(Terminal 2)$ docker container ls
CONTAINER ID   IMAGE        COMMAND                  CREATED         STATUS         PORTS     NAMES
f17bdfd41c3e   ros:humble   "/ros_entrypoint.sh …"   3 minutes ago   Up 3 minutes             festive_roentgen
```

If we create a file, destroy the container with `^d` or typing `exit` then run it again with the same command the file is no longer there.

## Part2: Docker 101

See Articulated Robotics video: https://www.youtube.com/watch?v=SAMPOK_lazw

### Installation

He recommends installing the docker engine using the convenience script from here: https://docs.docker.com/engine/install/ubuntu/

```bash
$ curl -fsSL https://get.docker.com -o get-docker.sh
$ sudo sh ./get-docker.sh
```

Then to prevent docker from running as `root` by default:

```bash
$ sudo groupadd docker
groupadd: group 'docker' already exists
$ sudo usermod -aG docker $USER
$ systemctl is-enabled docker
enabled
```

To enable if needed:

```bash
$ sudo systemctl enable docker.service
$ sudo systemctl enable containerd.service
```

Note adding user to the docker group requires logout and login / reboot to take effect.

And now it works:

```bash
$ docker run hello-world
```

General syntax is `$ docker base-command child-command` -. Some  common commands have short versions.

### Working with images with `docker image`

#### List images

```bash
$ docker image ls
$ docker images
```

#### Download an image from registry

```bash
$ docker image pull ros:humble
$ docker pull ros:humble
```

Identify the image as `<name or repository>:<tag or variant>` 

If you don't specify the tag -> it will download the latest. 

Default registry is DockerHub but can be changed

```bash
$ docker image pull ros:humble
$ docker pull ros:humble
```

If you try to run an image you don't have -> it will download it first

#### Delete an image

```bash 
$ docker image rm hello-world
$ docker rmi hello-world
```

need `-f`  force modifier if ever a container was run from this image:

```bash
$ docker image rm hello-world
```

### Working with containers with `docker container`

#### Run an image in a container

```bash
$ docker container run ros:humble
$ docker run ros:humble
```

This runs in a container, and by default quits when it finishes, which is OK for production. For development you want may a terminal, so add `-it` modifiers (give me a terminal and make it interactive):

```bash
$ docker run -it ros:humble 
```

#### List containers

```bash
$ docker container ls
$ docker ps
```

#### Stop a container

Type `^d` or `# exit` from inside or from outside:

```bash
$ docker container stop container_name
$ docker stop container_name
```

#### List all containers, even stopped ones

```bash
$ docker ps -a
```

#### Start a stopped container again

```bash
$ docker container start -i container_name
$ docker start -i container_name
```

Note this way previous changes persist

This is not the same as running another container from the same image, which starts anew (in a reset state)

```bash
$ docker run -it ros:humble 
```

#### Delete containers one by one

```bash
$ docker container rm container_name
```

#### Delete all stopped containers

```bash
$ docker container prune
```

#### Tips

* Run in container with custom name (`--name`) and delete automatically when finished (`--rm`):

```bash
$ docker run --rm --name my_ros_humble -it ros:humble
```

Network settings and passing hardware devices must be set up when creating the container

* Run another terminal of the same container

 Use `$ docker exec -it container_name command_to_execute` e.g. use a call to bash to simply open a terminal

```bash
$ docker exec -it my_ros /bin/bash
```

Or run a specific command inside the container e.g. 

```bash
$ docker exec -it my_ros ls
```

#### Docker files

How do we make permanent changes to an image so we don't lose config everytime we 

With Dockerfile we create a new custom image derived from an existing one.

Define the base image with `FROM`

Run terminal commands using `RUN` 

For example you can install things with `apt` (no need for `sudo` as everything runs by default as root). Note that images tend to be totally naked, without even a text editor.

To copy our custom files (code, sources, config files, dependencies etc) use `COPY`. Do not use `ADD` 

See example [here](./docker/Dockerfile).`

#### Build an image

`-t` to give the image a name

```bash
$ docker image build -t image_name path_to_dockerfile
$ docker build -t image_name path_to_dockerfile
```

In our example after building we have the image available and can run it in a container and inside it both the file  `my_config.yaml` and the app `nano` are available

```bash
$ docker build -t nano_image .
$ docker images
$ docker run -it nano_image
(root@container)$ nano robot_config/my_config.yaml
```

#### To share outside files 

Docker uses Volumes and Bind mounts (naming is ocassionally mixed causing confusion) which are kind of shared drives. 

He recommends Bind mounts.

Mount a host path to make it accessible from inside the container:

```bash
$ docker run -it -v absolute_path_on_host:absolute_path_on_image image_name
```

Now we can edit files in the host from the container!!!

The problem is that files created inside docker will be owned by `root` and will be difficult to handle by the user...

## Part 3

See Articulated Robotics video:  https://www.youtube.com/watch?v=RbP5cARP-SM

OS identify users by `username` and `UID`. You can see `username` and `group`with `ls -l` and `UID` and `GID` with `ls -ln`:

```bash
$ ls -l
-rw-r--r-- 1 mhered mhered  0 Oct 25 01:05 another_file.py
-rw-r--r-- 1 root   root   13 Oct 25 01:39 a_root_file
$ ls -ln
-rw-r--r-- 1 1000 1000  0 Oct 25 01:05 another_file.py
-rw-r--r-- 1    0    0 13 Oct 25 01:39 a_root_file
```

In ubuntu `root`'s UID is 0 and the default user's UID is 1000.

Groups are ways to give permissions to sets of users. Each user has a group (their primary group).

Often the system cares only about `UID` and `GID` not really `username` and `group`

To create a a non-root user with the same user id as the host user, add to the docker file: 

```bash
RUN groupadd --gid $USER_GID $USERNAME \
	&& useradd -s /bin/bash --uid $USER_UID --gid $USER_GID -m $USERNAME \
	&& mkdir /home/$USERNAME/.config \
	&& chown $USER_UID:$USER_GID /home/$USERNAME/.config
```

You can change the user to run different commands of the Dockerfile using `USER`. Useful e.g. to create files with certain permissions. 

The default user when container is run will be the last one set. Good practice to finish always with `USER root`.

You can override the user running when container starts with the `--user`parameter in the run command. E.g. this runs a `ros` (different name but same UID so same user for Linux) and mounts the path as mentioned earlier:

```bash
$ docker run -it --user ros -v $PWD/code/:/my_source_code nano_image
```

Can identify the user with either one of:

```
--user <username>
--user <username>:<group>
--user <uid>
--user <uid>:<gid>
```

Now files created from docker in the mount area will be owned by the default user in the host.

Note: it is not necessary, but sometimes it is useful to define the username inside container the same as in the host e.g. if we use paths that contain the username.

#### Set up `sudo`

Long command installs `sudo`, gives user `sudo` permission and allows using it without password:

```dockerfile
# Set up sudo: install sudo, add user to sudo group, allow sudo without password
RUN apt-get update \
    && apt-get install -y sudo \
    && echo $USERNAME ALL=\(root\) NOPASSWD:ALL > /etc/sudoers.d/$USERNAME \
    && chmod 0440 /etc/sudoers.d/$USERNAME \
    && rm -rf /var/lib/apt/lists/*

```

#### About `apt-get install` commands

* Why start every install with an `apt-get update`? Rebuilding docker images no guarantee all Dockerfile lines will be run so keep lines self sufficient. Also forced by the good practice of deleting the package lists after install.
* Why `apt-get` instead of `apt`? `apt` more user friendly not for automation. `apt-get` clunkier but more reliable for scripts

* Why `-y` on `apt-get-install`? to avoid prompting the user  for (Y/N) questions

* Why split commands in multiple lines separated by `\` ? so version control lets you track changes (otherwise it highlights the whole line!!). Recommended to order them alphabetically for easier reading

* why delete the package lists after install command? to save space in the image and forces people to run `apt-get update` before any install
* why all this these commands in a single `RUN` command? keeps image smaller and prevents errors
* sometimes you'll see also added setting`DEBIAN_FRONTEND=noninteractive` to prevent user prompts during install. He's not convinced does not add it but in any case not recommended to set it with `ENV`

### Basic Networking

To add basic networking capabilities just add to the docker run command the modifiers: `--network=host` to share networking with the host`--ipc=host` share shared memory with host.

```bash
$ docker image build -t nano_image . #rebuild image
$ docker run -it --user ros --network=host --ipc=host -v $PWD/code/:/my_source_code nano_image #run in container
```

## Specifying entry points and commands

When making a Dockerfile we can specify an entry point and a command

An entry point is a bash script in the same directory as the Dockerfile used to setup the runtime environment.

In the Dockerfile we `COPY` the file `entrypoint.sh` into the image, execute it with `ENTRYPOINT` and we can define default commands with `CMD`

If we provide extra arguments to the `docker run` command they replace the default command set with `CMD`:

```bash
$ docker run -it --user ros --network=host --ipc=host -v $PWD/code/:/my_source_code nano_image ros2 topic list
Provided arguments: ros2 topic list
/parameter_events
/rosout
$
```

It starts the container, execute the command and exit 
This allows to run a program being oblivious to the fact it is running in a container in a different OS and ROS version!!

## Graphics

 `ros:humble` is a lightweight ROS image, good for command line. 

Use instead `osrf/ros:humble-desktop-full` as base ROS image if you need graphics support.

It is complicated. There are different options for different applications

First need permission to access X. If you issue from inside the container issue you can give permission during the current session:

```bash
$ xhost + # give permission to all users
$ xhost +local: # give permission to all local users
$ xhost +local:root # give permission to root
```

Same commands with `-` revoke these permissions

Add a new volume and set environment variable same as for the host:

```bash
$ docker run -it --user ros \
--network=host --ipc=host \
-v $PWD/code/:/my_source_code  \
-v /tmp/.X11-unix:/tmp/.X11-unix:rw \
--env=DISPLAY \
nano_image 
```

Things to try if it does not work:

```bash
--gpus all
--runtime nvidia
--env="QT_X11_NO_MITSHM=1"
--env="NVIDIA_DRIVER_CAPABILITIES=all"
--env="NVIDIA_VISIBLE_DEVICES=all"
--device=/dev/dri:/dev/dri
```

Careful with the following, they are a security risk and should not be needed:

```bash
 --privileged
 --security-opt apparmor:unconfined
```

## Setting Locale and Time zones

Not needed if using official ros images as basis

Otherwise install language support and time zone support

## Autocompletion

Autocompletion should work when sourcing ROS but does not work if we do the source from the entrypoint, you actually need to type it manually which is inconvenient. 

A workaround: adding a simple `.bashrc` (which executes when launching a terminal) that includes the source commands for ROS then executing `entrypoint.sh`.

Create a `bashrc` in the same folder as the Dockerfile in host (without `.` for convenience) and then copy it into `/$HOME/.bashrc` in the container (the naming and location is compulsory)

Note there is another script you can also source from `.bashrc` to get autocompletion for `colcon` as well

Note it helps also installing `bash-completion` and `python3-argcomplete` (with a `RUN` command in Dockerfile)

## Part #4 Devices

https://www.youtube.com/watch?v=uf4zOigzTFo

Passing devices safely may be complex. 

"map all devices and run the container in `--privileged` mode" is bad advice, it exposes to security risks

### How linux handles devices

On Linux (almost) everything is a file, including (most) devices, i.e. Linux r/w from devices as if they were files. These files live in `/dev` folder

e.g. with `xxd` you get this a text output when moving the mouse

```bash
$ sudo xxd /dev/input/mouse2
00000000: 18fe 0118 fa04 18f6 0918 f40c 18f2 0e18  ................
00000010: f110 18f3 0d18 f20e 18f7 0b18 fc08 0800  ................
00000020: 0808 0203 0801 0108 0100 18ff 0038 fffd  .............8..
00000030: 38fe fb38 fcf6 38fe f938 fef9 38fd f938  8..8..8..8..8..8
00000040: fdf6 38fd f838 fdf4 38fd f638 fff8 38ff  ..8..8..8..8..8.
00000050: fc28 00fb 2800 fb28 02fd 0801 0008 0200  .(..(..(........
00000060: 0804 0208 0503 0806 0408 0503 0807 0508  ................
00000070: 0906 0805 0308 0403 0807 0508 0502 0802  ................
...
```

You can have more then one of these `dev` files acting as different interfaces to the same device, e.g. the mouse is also available at:

```bash
$ sudo xxd /dev/input/event15
00000000: 1746 3c65 0000 0000 09e6 0d00 0000 0000  .F<e............
00000010: 0200 0000 ffff ffff 1746 3c65 0000 0000  .........F<e....
00000020: 09e6 0d00 0000 0000 0200 0100 ffff ffff  ................
00000030: 1746 3c65 0000 0000 09e6 0d00 0000 0000  .F<e............
00000040: 0000 0000 0000 0000 1746 3c65 0000 0000  .........F<e....
00000050: 860d 0e00 0000 0000 0200 0000 f6ff ffff  ................
...
```

You can access them using slightly more descriptive links:

```bash
$ ls -l /dev/input/by-id
total 0
lrwxrwxrwx 1 root root  9 Mar 27  2023 usb-Chicony_Electronics_Co._Ltd._LG_Camera_0001-event-if00 -> ../event4
lrwxrwxrwx 1 root root 10 Oct 27 23:34 usb-Logitech_USB_Receiver-if01-event-kbd -> ../event14
lrwxrwxrwx 1 root root 10 Oct 27 23:34 usb-Logitech_USB_Receiver-if01-event-mouse -> ../event15
lrwxrwxrwx 1 root root  9 Oct 27 23:34 usb-Logitech_USB_Receiver-if01-mouse -> ../mouse2

```

Also we can id the drivers the OS is trying to use to talk to the devices:

```bash
$ ls -l /dev/input
total 0
drwxr-xr-x 2 root root      60 Oct 28 06:50 by-id
drwxr-xr-x 2 root root     140 Oct 28 06:50 by-path
crw-rw---- 1 root input 13, 64 Mar 27  2023 event0
crw-rw---- 1 root input 13, 65 Mar 27  2023 event1
crw-rw---- 1 root input 13, 74 Mar 27  2023 event10
crw-rw---- 1 root input 13, 75 Oct 22 21:27 event11
crw-rw---- 1 root input 13, 76 Mar 27  2023 event12
crw-rw---- 1 root input 13, 77 Oct 22 21:27 event13
crw-rw---- 1 root input 13, 81 Oct 28 08:09 event17
crw-rw---- 1 root input 13, 66 Mar 27  2023 event2
crw-rw---- 1 root input 13, 67 Mar 27  2023 event3
crw-rw---- 1 root input 13, 68 Mar 27  2023 event4
crw-rw---- 1 root input 13, 69 Mar 27  2023 event5
crw-rw---- 1 root input 13, 70 Mar 27  2023 event6
crw-rw---- 1 root input 13, 71 Mar 27  2023 event7
crw-rw---- 1 root input 13, 72 Mar 27  2023 event8
crw-rw---- 1 root input 13, 73 Mar 27  2023 event9
crw-rw---- 1 root input 13, 63 Mar 27  2023 mice
crw-rw---- 1 root input 13, 32 Mar 27  2023 mouse0
crw-rw---- 1 root input 13, 33 Mar 27  2023 mouse1

```

the numbers `13, 64` in the 3rd line are the major ID (`13` is input devices) and minor driver ID (64 for mouse)

Documentation at: www.kernel.org/doc/Documentation/admin-guide/devices.txt

### Connecting a USB gamepad

In the docker file we use a `RUN` command to install a few programs for device testing: `evtest`, `jstest-gtk` and ` python3-serial ` 

Even if I mount devices the container won't see them. Need to provide extra info that this is a device not a file. If you know your device address and it is fixed we can add to the run command the argument `--device=/dev/input/js0`:

```bash
$ docker run -it --user ros --network=host --ipc=host -v $PWD/code/:/my_source_code  -v /tmp/.X11-unix:/tmp/.X11-unix:rw --env=DISPLAY --device=/dev/input/js0 nano_image 
```

This is limited: supports plugging and unplugging BUT is brittle: needs to have the device connected when the container starts, runs, stops and restarts, and will stop working if the address changes. Also this uses the old joy dev driver which does not work with ROS

A better way: tell Docker it is allowed to control devices using certain driver types. Bind mounting `/dev/input` then specify a device C-group rule for input devices (`13`) with read, make node (??) and write options as follows:

```bash
$ docker run -it --user ros --network=host --ipc=host -v $PWD/code/:/my_source_code  -v /tmp/.X11-unix:/tmp/.X11-unix:rw --env=DISPLAY -v /dev/input/:/dev/input/ --device-cgroup-rule='c 13:* rmw' nano_image 
```

You could be more general and allow control for all devices with: `-v /dev:/dev --device-cgroup-rule='c *:* rmw' `

### Connecting a camera

List USB devices:

```bash
$ lsusb
Bus 004 Device 001: ID 1d6b:0003 Linux Foundation 3.0 root hub
Bus 003 Device 004: ID 27c6:6a94 Shenzhen Goodix Technology Co.,Ltd. Goodix USB2.0 MISC
Bus 003 Device 009: ID 050d:008a Belkin Components 
Bus 003 Device 007: ID 046d:c534 Logitech, Inc. Unifying Receiver
Bus 003 Device 010: ID 05e3:0751 Genesys Logic, Inc. microSD Card Reader
Bus 003 Device 008: ID 2109:0102 VIA Labs, Inc. HD Webcam C525
Bus 003 Device 006: ID 1a40:0101 Terminus Technology Inc. Hub
Bus 003 Device 003: ID 2109:2817 VIA Labs, Inc. USB2.0 Hub             
Bus 003 Device 002: ID 04f2:b6fa Chicony Electronics Co., Ltd LG Camera
Bus 003 Device 005: ID 8087:0026 Intel Corp. 
Bus 003 Device 011: ID 046d:0826 Logitech, Inc. HD Webcam C525
Bus 003 Device 001: ID 1d6b:0002 Linux Foundation 2.0 root hub
Bus 002 Device 003: ID 0bda:8153 Realtek Semiconductor Corp. RTL8153 Gigabit Ethernet Adapter
Bus 002 Device 002: ID 2109:0817 VIA Labs, Inc. USB3.0 Hub             
Bus 002 Device 001: ID 1d6b:0003 Linux Foundation 3.0 root hub
Bus 001 Device 001: ID 1d6b:0002 Linux Foundation 2.0 root hub

```

List cameras:

```bash
$ ls -ltrh /dev/video*
crw-rw----+ 1 root video 81, 1 Mar 27  2023 /dev/video1
crw-rw----+ 1 root video 81, 0 Mar 27  2023 /dev/video0
crw-rw----+ 1 root video 81, 3 Dec 15 00:25 /dev/video3
crw-rw----+ 1 root video 81, 2 Dec 15 00:25 /dev/video2
```

Tried checking the camera with cheese as described here: https://linuxconfig.org/how-to-test-webcam-on-ubuntu-22-04-jammy-jellyfish but it does not work, see discussion here: https://discourse.articulatedrobotics.xyz/t/discussion-docker-and-devices-docker-for-robotics-pt-4/552/5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

I then tried with `guvcview`: see here about installation https://howtoinstall.co/package/guvcview and a tutorial (in Spanish): https://www.youtube.com/watch?v=3-ZoJnqiZIk

In the docker file install with a `RUN` command the following packages: `usbutils` , `guvcview` and `dbus-x11`.

Rebuild the image (from the folder where the dockerfile lives):

```bash
$ docker image build -t nano_image .
```

Then run the container with:

```bash
$ docker run -it --user ros --network=host --ipc=host -v $PWD/code/:/my_source_code:rw  -v /tmp/.X11-unix:/tmp/.X11-unix:rw -v $PWD/data:/my_data:rw --env=DISPLAY --device=/dev/video0 --device=/dev/video1 --device=/dev/video2 --device=/dev/video3 --device=/dev/dri/card0 nano_image
```

And the camera with

```bash
(container)$ guvcview -d /dev/video2
```

For some reason it was running with `root` not my user, so no permission to write files. but it worked well after rebuilding the image.

#### Notes

* Still several errors present. 
* `guvcview` insists searching for video0 and video1
* One of the camera devices (`video3`?) does not work. 

### Connecting a depth camera

### Connecting a serial device

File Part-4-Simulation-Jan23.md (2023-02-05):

# Prerequisites

- [x] installed ROS (See video [Getting Ready for ROS Part 3: Installing ROS](https://articulatedrobotics.xyz/ready-for-ros-3-installing-ros/) and cfr. my notes in [Part-1-Getting-ready-ROS2-Aug22-Jan23.md](Part-1-Getting-ready-ROS2-Aug22-Jan23.md))

- [x] watched Intro video [Why do I think you should build this robot?](https://www.youtube.com/watch?v=OWeLUSzxMsw&t=0s)

  - [x] copied template from github: https://github.com/joshnewans/my_bot, created a workspace and built with colcon:
  
  ```bash
  $ cd ~ 
  $ mkdir dev_ws && cd dev_ws
  $ mkdir src && cd src
  $ git clone https://github.com/mhered/manolobot_uno.git
  $ cd ..
  $ colcon build --symlink-install
  ```
  
- [x] watched TF overview video: [ROS Transform System (TF) | Getting Ready to Build Robots with ROS #6](https://www.youtube.com/watch?v=QyvHhY4Y_Y8&t=0s). See my notes in [Part-1-Getting-ready-ROS2-Aug22-Jan23.md](Part-1-Getting-ready-ROS2-Aug22-Jan23.md)

  * [x] installed xacro and joint state publisher GUI

- [x] watched URDF Overview video [How do we describe a robot? With URDF! | Getting Ready to build Robots with ROS #7](https://www.youtube.com/watch?v=CwdbsvcpOHM). See my notes in [Part-1-Getting-ready-ROS2-Aug22-Jan23.md](Part-1-Getting-ready-ROS2-Aug22-Jan23.md)

# Describing the robot in URDF



Video: [Creating a rough 3D model of our robot with URDF](https://youtu.be/BcjHyhV0kIs) 
Blog: [Making a Mobile Robot #2 - Concept Design URDF](https://articulatedrobotics.xyz/mobile-robot-2-concept-urdf/) 
Discussion: [Discourse](https://discourse.articulatedrobotics.xyz/t/discussion-concept-design-urdf-making-a-mobile-robot-pt-2/27) 

---

* root link must be called `base_link`
* orientation is:

  - x forward (red)

  - y left (green)

  - z up (blue)

3 things to take into consideration when saving changes in URDF:

1. build workspace with `$ colcon build --symlink-install`. This avoids having to rebuild with every change (except if you add new files)

2. quit (ctrl+c) and relaunch the robot state publisher with. `$ ros2 launch manolobot rsp.launch.py`every time you make a change

3. click **Reset** to refresh RVIZ so it picks up changes. If this does not work tick/untick display items or close/reopen as last resource

1. To get started, go to the workspace and source it:

```bash
(Terminal 1):$ cd dev_ws
$ source install/setup.bash
```

2. With every change run the launch file:

```bash
$ ros2 launch manolobot_uno rsp.launch.py
```

If new files are present rebuild the workspace with `colcon` before the launch file:

```
$ colcon build --symlink-install
```

3. to view run RVIZ in another terminal

```bash
(Terminal 2):$ rviz2 -d dev_ws/src/manolobot_uno/config/view_bot.rviz
```

4. to publish dynamic joints run `joint_state_publisher_gui` in another terminal 

```bash
(Terminal 3):$ ros2 run joint_state_publisher_gui joint_state_publisher_gui
```

To save the state of RVIZ: Save as... in `./config/view_bot.rviz` then open rviz with the rviz file as parameter:

```bash
$ rviz2 -d dev_ws/src/manolobot_uno/config/view_bot.rviz
```

# Merging `manolobot_uno` into the main repo `manolobot` 

Based on **The good way to download code from internet**, see [notes on ETH Zurich course](https://github.com/mhered/ROS-notes/blob/main/ROS-notes/ROS_ETH_Zurich_L1.md). 

Rather than having multiple repos I copy the folder into the main one and symlink to `dev_ws/src`. 

This is way cleaner:

1. copy the contents of the repo to a folder inside `manolobot`

```bash
$ mv ~/dev_ws/src/manolobot_uno ~/manolobot/
```

2. Symlink it to `dev_ws`

```bash
$ ln -s ~/manolobot/manolobot_uno/ ~/dev_ws/src/
```

3. Build it and re-source environment

```bash
$ colcon build --symlink-install
$ cd ~/dev_ws
$ source install/setup.bash
```

4. Then, to launch the `robot_state_publisher`:

```bash
$ ros2 launch manolobot_uno rsp.launch.py
```

# Simulating the robot in Gazebo

Blog: https://articulatedrobotics.xyz/mobile-robot-3-concept-gazebo/

Check also: https://articulatedrobotics.xyz/ready-for-ros-8-gazebo/

1. Launch `robot_state_publisher` with sim time:

```bash
(Terminal 1):$ ros2 launch manolobot_uno rsp.launch.py use_sim_time:=true
```

2. Install - if not done before - and launch gazebo with ROS compatibility:

```bash
$ sudo apt install ros-foxy-gazebo-ros-pkgs
(Terminal 2):$ ros2 launch gazebo_ros gazebo.launch.py
```

3. Spawn the robot:

```bash
(Terminal 3):$ ros2 run gazebo_ros spawn_entity.py -topic robot_description -entity manolobot
```

Prepared  [launch_sim.launch.py](./manolobot_uno/launch/launch_sim.launch.py) to achieve the same effect (launch gazebo and spawn the robot) but with a single command:

```bash
(Terminal 1):$ ros2 launch manolobot_uno launch_sim.launch.py
```

* Created`gazebo_control.xacro` , a new file with the configuration of the `diff_drive` plugin for gazebo

* Properties definition (robot dimensions etc) need to be used now as well by `gazebo_control.xacro` so I moved their definition from `robot_core.xacro` to a separate file `properties.xacro`  and included it from `robot.urdf.xacro`.

* Modified `robot.urdf.xacro`to add calls to both `properties.xacro` and `gazebo_control.xacro`

* Modified `robot_core.xacro`:

  * added gazebo tags to define colors for each link

  * added very low friction coefficients mu1 mu2 for caster wheels

With this it is possible to control the robot in the simulation using `teleop_key`:

```bash
(Terminal 2):$ ros2 run teleop_twist_keyboard teleop_twist_keyboard
```

* Adjusted the masses to get a proper behavior of the simulation. **Note: the values are not real ones, need to make measurements!!**
* Created launch file `joystick.launch` and parameter file `joystick.yaml` to configure and launch support for PS4 gamepad as follows: 
  *  Dead man switches: L button (left shoulder) for normal speed, R button (right shoulder) for turbo
  * Control on left stick: vertical axis for forward/backward motion and horizontal axis for rotation. 
* See details of the setup of the gamepad in [./BOM/gamepad.md](./BOM/gamepad.md)

Launch with:

```bash
(Terminal 2):$ ros2 launch manolobot_uno joystick.launch.py
```

* Driving `manolobot_uno` around in Gazebo:



# Tips & tricks

* to open Gazebo in a world:

```bash
(Terminal 1):$ ros2 launch manolobot_uno launch_sim.launch.py world:=./src/manolobot_uno/worlds/cones.world use_sim_time:=true
```

* to force Gazebo to update changes in the model: close all other terminals, source, if necessary kill hung up processes with:

```bash
$ sudo killall -9 gazebo gzserver gzclient
```

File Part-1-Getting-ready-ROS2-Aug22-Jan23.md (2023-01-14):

# Articulated Robotics - Getting Ready for ROS series 

[Getting ready to Build Robots with ROS youtube playlist](https://www.youtube.com/playlist?list=PLunhqkrRNRhYYCaSTVP-qJnyUPkTxJnBt)

8+1 videos covering the setup and an overview of ROS2, TF, URDF and gazebo

## (#01) What we need 

Link to blog post: [Getting Ready for ROS Part 1: What you need](https://articulatedrobotics.xyz/ready-for-ros-1-what-you-need/)

### Skills

Basic Admin: install and configure OS
Move around in Linux
Git for version tracking
Programming & Compiling
Basic electronics: programming an arduino, soldering, connecting a breadboard

### Hardware setup
How to balance small, low energy, powerful and cheap? split computing between 2 paired computers:
* a small onboard computer on the robot (RPi): takes sensor data, sends for processing over network to base station. Receives results and send signals to actuators
* a powerful off-board base station and development machine (mid-range laptop): runs algorithms for processing, takes joystick input, provides visualization and doubles as development machine for coding comfotsably

Docker and virtual machines are fiddly better full Ubuntu installation

### Software
- [x] LTS ROS 2 Foxy Fitzroy is compatible with Ubuntu 20.04 focal fossa (ubuntu mate 64 bits https://ubuntu-mate.org/download). Today latest is ROS 2 Humble and Ubuntu 22.04 Jellyfish.

- [x] version control sfw: git in both rpi and laptop

``` bash
$ sudo apt install git
```
- [x] code editor: vscode only needed on laptop

``` bash
$ sudo snap install --classic code
```
- [x] recommended install also VS code [remote development extension pack](https://code.visualstudio.com/docs/remote/ssh) to code on RPi without a screen

- [x] arduino IDE on both computers ([instructions](https://docs.arduino.cc/software/ide-v1/tutorials/Linux)):
  - [x] Download [ARM Linux 64 bits](https://downloads.arduino.cc/arduino-1.8.19-linuxaarch64.tar.xz) and [Linux 64 bits](https://downloads.arduino.cc/arduino-1.8.19-linux64.tar.xz) versions of IDE 1.8.19 from the [Arduino download page](https://www.arduino.cc/en/software)
  - [x] On laptop, extract to a suitable location e.g. `~/Applications/arduino-1.8.19/`
  - [x] From inside the folder,  run the install script that creates desktop links:
  
  ```bash
     $ sudo sh install.sh
  ```
  
  - [x] Open the IDE, under **Tools** select **Board:"Arduino Nano"**, **Processor:"ATmega328P (OldBootloader)"** and **Port:"/dev/ttyUSB0"**. Note: choosing the wrong processor gives [this error](https://support.arduino.cc/hc/en-us/articles/4401874331410#avrdude-stk500_recv-and-stk500_getsync)
  
  arduino_setup
  
  - [x] If it still does not connect add the user to the `dialout` group:
  
  ```
  $ ls -l /dev/ttyUSB*
  crw-rw---- 1 root dialout 188, 0 Nov 20 13:47 /dev/ttyUSB0
  $ sudo usermod -a -G dialout <username>
  ```
  
  Tested with **Blink** and **AnalogReadSerial** under **File -> Examples -> 01.Basics** 

### Other tools
- [x] 12V bench power supply
- [ ] Battery charger
- [x] Multimeter
- [x] Soldering iron and solder
- [x] Crimp tools, screwdrivers, Pliers, tieraps, screws,
- [x] rotary tool
- [ ] 3D printer

## (#02) Network setup
Link to blog post: [Getting Ready for ROS Part 2: Networking](https://articulatedrobotics.xyz/ready-for-ros-2-networking/)

Network is needed to remotely control our robot, have robots work together and split computation over multiple machines. ROS provides the protocols, we just need to ensure all computers are in the same network. Requisites:

* Fast reliable connection between robot and laptop
* Internet access to install sfw and back-up in git
* Control over the network e.g. to set up fixed IP addresses

3 options for architecture:

* Existing network: rpi and laptop connected to the router. Easy but not portable, lacks control (DHCP/static IP, network congestion, dropouts etc), may lead to ROS conflicts when using more than one robot
* Access point network: configure laptop to generate wifi network, robot connects to it. Flexible but requires effort to configure, a second wifi card, complex with more than one base computer.
* Dedicated network with a travel router. Preferred.

- [x] Install `ssh` on RPi using keyboard mouse and monitor

```bash
(RPi):$ sudo apt install openssh-server
```

- [x] Get the local IP address of RPi with

```bash
(RPi):$ ip addr
```

- [x] To access RPi terminal remotely from laptop:

```bash
(laptop):$ ssh <pi_username>@<pi_ip_address> # in particular ssh mhered@192.168.8.105

```
- [ ] Write a config file with [`netplan`](https://netplan.io) **Note: my laptop does not have Ethernet port!**

Other tools:

* `scp` for file transfer
* X forwarding to run GUIs remotely
* VS code [remote development extension pack](https://code.visualstudio.com/docs/remote/ssh)

## (#03) Install ROS

Link to blog post: [Getting Ready for ROS Part 3: Installing ROS](https://articulatedrobotics.xyz/ready-for-ros-3-installing-ros/)
Install ROS on both `laptop` and `RPi`:

- [X] Check UTF-8 is set and that the Ubuntu universe repo is enabled with: 
```bash
$ locale
...
$ apt-cache policy | grep universe
```
The second should result in something like:
```
500 http://ports.ubuntu.com/ubuntu-ports focal/universe arm64 Packages
     release v=20.04,o=Ubuntu,a=focal,n=focal,l=Ubuntu,c=universe,b=arm64
```
Note: cfr. the [ROS Foxy installation guide](https://docs.ros.org/en/foxy/Installation/Ubuntu-Install-Debians.html) if more details needed. 
- [X] Add ROS2 apt repo to the system with:
```bash
$ sudo apt update && sudo apt install curl gnupg2 lsb-release
$ sudo curl -sSL https://raw.githubusercontent.com/ros/rosdistro/master/ros.key  -o /usr/share/keyrings/ros-archive-keyring.gpg
$ echo "deb [arch=$(dpkg --print-architecture) signed-by=/usr/share/keyrings/ros-archive-keyring.gpg] http://packages.ros.org/ros2/ubuntu $(source /etc/os-release && echo $UBUNTU_CODENAME) main" | sudo tee /etc/apt/sources.list.d/ros2.list > /dev/null
```
- [X] Install `ros2` and `colcon` and add sourcing of the ROS2 environment to `~/.bashrc` with:
```bash
$ sudo apt update && sudo apt upgrade
$ sudo apt install ros-foxy-desktop
$ sudo apt install python3-colcon-common-extensions
$ echo "source /opt/ros/foxy/setup.bash" >> ~/.bashrc
$ source ~/.bashrc
```

- [X] Test communication between a node written in C++ running on the laptop and a python node running on RPi: 
```bash
(laptop:)$ ros2 run demo_nodes_cpp talker
...
[INFO] [1662750396.990408713] [talker]: Publishing: 'Hello World: 67'
[INFO] [1662750397.990414028] [talker]: Publishing: 'Hello World: 68'
[INFO] [1662750398.990288416] [talker]: Publishing: 'Hello World: 69'
...
```
```bash
(RPi:)$ ros2 run demo_nodes_py listener
...
[INFO] [1662750392.965285945] [listener]: I heard: [Hello World: 63]
[INFO] [1662750393.965151014] [listener]: I heard: [Hello World: 64]
[INFO] [1662750394.965403701] [listener]: I heard: [Hello World: 65]
...
```
Success!

## (#04) 10 concepts about ROS

Link to blog post: [Getting Ready for ROS Part 4: ROS Overview (10 concepts you need to know)](https://articulatedrobotics.xyz/ready-for-ros-4-ros-overview/)

1. ROS Distributions
2. Nodes
3. Topics and Messages
4. Services
5. Node Arguments (Parameters and Remapping)
6. Launch Files
7. Packages
8. System Install (the underlay)
9. Workspaces/Overlays
10. QoS

## (#05) Create a package

Link to blog post: [Getting Ready for ROS Part 5: Making your First Package](https://articulatedrobotics.xyz/ready-for-ros-5-packages/)

1. Create a workspace 
2. Create a package
3. Build it
4. Upload to git
5. Pull from git to the robot
6. Test it 

## (#06) The Transform System (TF)

Link to blog post: [Getting Ready for ROS Part 6: The Transform System (TF)](https://articulatedrobotics.xyz/ready-for-ros-6-tf/)

* Played with static transforms: `$ ros2 run tf2_ros static_transform_publisher x y z yaw pitch roll parent_frame child_frame` with translations and rotations (in radians) processed in the order they appear in the command.

* to open RVIZ: `$ ros2 run rviz2 rviz2` or simply `$ rviz2`

* install xacro and joint state publisher GUI:

  ```bash
  $ sudo apt install ros-foxy-xacro ros-foxy-joint-state-publisher-gui
  ```

* play with dynamic transforms

  - `robot_state_publisher` node takes URDFs and publishes transforms in `/tf` and `/tf_static` topics. We need to publish `/joint_states` messages e.g. using `joint_state_publisher_gui`

  - It takes as parameter the complete contents (!) of the URDF file, which is why we add `"$( xacro /path-to-file )"`:

```bash
(Terminal 1):$ ros2 run robot_state_publisher robot_state_publisher --ros-args -p robot_description:="$( xacro ~/example_robot.urdf.xacro )"
```

```bash
(Terminal 2):$ ros2 run joint_state_publisher_gui joint_state_publisher_gui
```

* tried debugging with `view_frames`

  * Similar to `rqt_tf_tree` from ROS1, which does not work in ROS2
  * Run `view_frames` with:

  ```bash
  $ ros2 run tf2_tools view_frames.py
  ```

  * Listens to transforms 5 secs then writes a `frames.gv` and `frames.pdf` to the local directory

## (#07) Describing a robot with URDF

Link to blog post: [Getting Ready for ROS Part 7: Describing a robot with URDF](https://articulatedrobotics.xyz/ready-for-ros-7-urdf/)

* URDF: Unified Robot Description Format, based on XML

* Describes the robot as a tree of **Links** connected by **Joints** - where each Link may have many childs but has only one parent (tree structure without closed loops)
* Root tag of the XML is `robot`, its only attribute is `name`
* We assign a **Link** to every part that moves relative to others or can be physically detached (hence will require calibration). A **Link** is defined by a `name` and also its `visual`, `collision` and `inertial` properties. We can define multiple `visual`, `collision` tags to define complex shapes.
* **Joints** define the position and orientation of the child with respect to the parent Link. 4 most common Joint types are `revolute` (rotate with limits), `continuous` (rotate freely), `prismatic` (linear slider) and  `fixed`. a **Joint** is defined by `name`,` type`, `parent` and `child`, `origin` (initial position),  and for non fixed joints also`axis`, and `limits` (`min`and `max` are position in rad or m, `velocity` is max in rad/s or m/s and `effort` is max in N or Nm). 
* Naming convention: `arm_link` is the child link in`arm_joint`

```xml
<?xml xmlns:xacro="http://www.ros.org/wiki/xacro" version="1.0"?>
<robot name="example_urdf">
    <!-- example Link -->
    <link name="base_link">
    	<visual> what we see in RVIZ and gazebo
            <geometry></geometry> overall shape: box, cylinder, sphere or path to 3d mesh 
            <origin></origin> offset to geometry. Origin can be selected freely except for rotating Links that must have origin at pivot point.
            <material></material> color as RGB triplet or name of one defined previously 
        </visual>
        <collision> used for physics collision calculations. Copy & paste of visual or simplified for better performance.
            <geometry></geometry>
            <origin></origin>
        </collision>
        <inertial> for calculations of response to forces
            <mass></mass>
            <origin></origin> center of mass
            <inertia></inertia> rotational inertia matrix. approximated from primitives or calculated with CAD program for meshes
        </inertial>
    </link>
    
    <!-- example Joint -->
    <joint name="arm_joint" type = "revolute">
        <parent link="slider_link" />
        <child link="arm_link" />
        <origin xyz="0.25 0 0.12" rpy="0 0 0" />
        <axis xyz="0 -1 0" />
        <limit lower="0" upper="${pi/2}" velocity="100" effort="100">
    </joint>

</robot>
```

* `xacro` XML macro allows to include subfiles in a main file e.g to split into smaller reusable files. To enable it add `xmlns:xacro="http://www.ros.org/wiki/xacro"` to the `robot` tag. The include statement is e.g.: `<xacro:include filename="my_materials.xacro" />`

* That's why we normally process the raw URDF file(s) with xacro and feed it directly to the `robot_state_publisher` 

* Also has properties and mathematical operators e.g.  `<xacro:property name="r" value ="0.5" />` used later to define a cylinder  `<cylinder radius="${r}" length="${4*r}">`

* Also has macros that expand replacing parameters, e.g.:

  ```xml
  <xacro:macro name="inertial_box" params ="mass x y z *origin">
      <inertial>
          <xacro:insert_block name="origin" />
          <mass value="${mass}" />
          <inertia ixx="${(1/12) * mass * (y*y+z*z)}" etc />
      </inertial>
  </xacro:macro>
  ```

  Can be used as:

  ```xml
  <xacro:inertial_box mass="12" x="2" y="3" z="4">
      <origin xyz="0 2 4" rpy="0 0 0" />
  </xacro:inertial_box>
  ```

  And expands to:

  ```
      <inertial>
          <origin xyz="0 2 4" rpy="0 0 0" />
          <mass value="12" />
          <inertia ixx="25" etc />
      </inertial>
  ```

## (#08) Simulating with Gazebo

Link to blog post: [Getting Ready for ROS Part 8: Simulating with Gazebo](https://articulatedrobotics.xyz/ready-for-ros-8-gazebo/)

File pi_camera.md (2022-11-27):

Tutorial: https://larrylisky.com/2016/11/24/enabling-raspberry-pi-camera-v2-under-ubuntu-mate/ rather old, from 2016

https://wesleych3n.medium.com/enable-camera-in-raspberry-pi-4-with-64-bit-ubuntu-21-04-d97ce728db9d

Note: Connect ribbon with blue side facing the USB connectors

```bash
(RPi)$ sudo apt-get update
(RPi)$ sudo apt-get upgrade
```

Installation of `raspi-config` failed

```bash
(RPi)$ sudo apt-get install raspi-config rpi-update
Reading package lists... Done
Building dependency tree       
Reading state information... Done
E: Unable to locate package raspi-config
E: Unable to locate package rpi-update
```

On the other hand the file `/boot/firmware/config.txt` already had the lines:

```
start_x=1
gpu_mem=128
```

`/dev(video0/` was detected:

```bash
$ ls -ltrh /dev/video*
crw-rw----+ 1 root video 81, 0 Apr 21  2022 /dev/video13
crw-rw----+ 1 root video 81, 1 Apr 21  2022 /dev/video10
crw-rw----+ 1 root video 81, 2 Apr 21  2022 /dev/video14
crw-rw----+ 1 root video 81, 4 Apr 21  2022 /dev/video16
crw-rw----+ 1 root video 81, 3 Apr 21  2022 /dev/video15
crw-rw----+ 1 root video 81, 7 Apr 21  2022 /dev/video12
crw-rw----+ 1 root video 81, 6 Apr 21  2022 /dev/video0
crw-rw----+ 1 root video 81, 5 Apr 21  2022 /dev/video11

```

And `cheese` was already installed

I tested with `cheese`  (cfr. https://linuxconfig.org/how-to-test-webcam-on-ubuntu-20-04-focal-fossa) and the camera works but is very slow, has low resolution, and weird colors.

This article: https://raspberrypi.stackexchange.com/questions/114035/picamera-and-ubuntu-20-04-arm64 recommends using `opencv` but mentions there is active development to support `libcamera`? in ubuntu arm 64b.

However this guy claims `raspiconfig` can be installed in Ubuntu Mate: https://ubuntu-mate.community/t/install-raspi-config-on-ubuntu-mate-20-10-and-higher/23974

To be continued...

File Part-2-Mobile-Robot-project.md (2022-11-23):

# Articulated Robotics - Mobile Robot series 

15 videos and counting, with companion blog posts, covering hardware and software design, simulation, operation, etc

| Video # | Playlist: [Building a mobile robot](https://www.youtube.com/playlist?list=PLunhqkrRNRhYAffV8JDiFOatQXuU-NnxT) | Video duration | Blog: [Articulated Robotics](https://articulatedrobotics.xyz/) | Comments |
| ----- | --- | --- | --- | --- |
| 1 | [Why do I think you should build this robot?](https://youtu.be/OWeLUSzxMsw) | 15:54 | [Making a Mobile Robot #1 - Project Overview](https://articulatedrobotics.xyz/mobile-robot-1-project-overview/) | |
| 2 | [Creating a rough 3D model of our robot with URDF](https://youtu.be/BcjHyhV0kIs) | 27:18 | [Making a Mobile Robot #2 - Concept Design URDF](https://articulatedrobotics.xyz/mobile-robot-2-concept-urdf/) | |
| 3 | [Driving your virtual robot!](https://youtu.be/IjFcr5r0nMs) | 22:57 | [Making a Mobile Robot #3 - Concept Design Gazebo](https://articulatedrobotics.xyz/mobile-robot-3-concept-gazebo/) | |
| 4 | [Giving Our Robot a Brain - Raspberry Pi](https://youtu.be/RAqFgU3Gfv0) | 6:59 | [Making a Mobile Robot #4 - Raspberry Pi](https://articulatedrobotics.xyz/mobile-robot-4-raspberry-pi/) | |
| 5 | [EVERYTHING you need to know about about robot power](https://youtu.be/Iye4uVLmj8o) | 16:33 | [Making a Mobile Robot #5 - Power Concepts](https://articulatedrobotics.xyz/mobile-robot-5-power-theory/) | |
| 6 | [Robot Power 2: Electric Boogaloo](https://youtu.be/_FGYVgAti9M) | 14:04 | No Blog post | |
| 7 | [The Ultimate Guide to using Motors in Robotics (including ROS, Raspberry Pi)](https://youtu.be/-PCuDnpgiew) | 25:56 | No Blog post | |
| 8 | [How do we add LIDAR to a ROS robot?](https://youtu.be/eJZXRncGaGM) | 22:45 | [Making a Mobile Robot #8 - Adding a Lidar](https://articulatedrobotics.xyz/mobile-robot-8-lidar/) | |
| 9 | [How to use Cameras in ROS (Sim Camera and Pi Camera)](https://youtu.be/A3nw2M47K50) | 32:01 | [Making a Mobile Robot #9 - Adding a Camera](https://articulatedrobotics.xyz/mobile-robot-9-camera/) | |
| 10 | [How to get your robot to see in 3D! (Depth Cameras in ROS)](https://youtu.be/T9xZ22i9-Ys?list=PLunhqkrRNRhYAffV8JDiFOatQXuU-NnxT) | 23:21 | No blog post | |
| 11 | [Designing a chassis for our robot! (+ other fixes)](https://youtu.be/RjhBRn6lDSM) | 16:11 | No blog post | |
| 12 | [Solving the problem EVERY robot has (with ros2_control)](https://youtu.be/4QKsDf1c4hc) | 24:36 | [Making a Mobile Robot #12 - ros2_control Concept & Simulation](https://articulatedrobotics.xyz/mobile-robot-12-ros2-control/) | |
| 13 | [Ros2_control Extra Bits](https://youtu.be/8ByoP_oSdno) | 17:38 | [Making a Mobile Robot #12a - ros2_control extra bits](https://articulatedrobotics.xyz/mobile-robot-12a-ros2-control-extra/) | |
| This video is not in the playlist | [Using ros2_control to drive our robot (off the edge of the bench...)](https://youtu.be/4VVrTCnxvSw) | 31:37 | [Making a Mobile Robot #13 - Using ros2_control on a real robot](https://articulatedrobotics.xyz/mobile-robot-13-ros2-control-real/) |  |
| 14 | [Easy wireless control for your homemade robot!](https://youtu.be/F5XlNiCKbrY) | 21:44 | [Making a Mobile Robot #14a - Teleoperation](https://articulatedrobotics.xyz/mobile-robot-14a-teleop/) | |
| 15 | [Control your ROS robot from your phone!](https://youtu.be/hkkG-Sgi9Sk) | 21:05 | [Making a Mobile Robot #14b - Advanced Teleop](https://articulatedrobotics.xyz/mobile-robot-14b-adv-teleop/) | |

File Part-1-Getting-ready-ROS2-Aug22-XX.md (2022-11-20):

# Articulated Robotics - Getting Ready for ROS series 

[Getting ready to Build Robots with ROS youtube playlist](https://www.youtube.com/playlist?list=PLunhqkrRNRhYYCaSTVP-qJnyUPkTxJnBt)

8+1 videos covering the setup and an overview of ROS2, TF, URDF and gazebo

## (#01) What we need 

Link to blog post: [Getting Ready for ROS Part 1: What you need](https://articulatedrobotics.xyz/ready-for-ros-1-what-you-need/)

### Skills

Basic Admin: install and configure OS
Move around in Linux
Git for version tracking
Programming & Compiling
Basic electronics: programming an arduino, soldering, connecting a breadboard

### Hardware setup
How to balance small, low energy, powerful and cheap? split computing between 2 paired computers:
* a small onboard computer on the robot (RPi): takes sensor data, sends for processing over network to base station. Receives results and send signals to actuators
* a powerful off-board base station and development machine (mid-range laptop): runs algorithms for processing, takes joystick input, provides visualization and doubles as development machine for coding comfotsably

Docker and virtual machines are fiddly better full Ubuntu installation

### Software
- [x] LTS ROS 2 Foxy Fitzroy is compatible with Ubuntu 20.04 focal fossa (ubuntu mate 64 bits https://ubuntu-mate.org/download). Today latest is ROS 2 Humble and Ubuntu 22.04 Jellyfish.

- [x] version control sfw: git in both rpi and laptop

``` bash
$ sudo apt install git
```
- [x] code editor: vscode only needed on laptop

``` bash
$ sudo snap install --classic code
```
- [x] recommended install also VS code [remote development extension pack](https://code.visualstudio.com/docs/remote/ssh) to code on RPi without a screen

- [x] arduino IDE on both computers ([instructions](https://docs.arduino.cc/software/ide-v1/tutorials/Linux)):
  - [x] Download [ARM Linux 64 bits](https://downloads.arduino.cc/arduino-1.8.19-linuxaarch64.tar.xz) and [Linux 64 bits](https://downloads.arduino.cc/arduino-1.8.19-linux64.tar.xz) versions of IDE 1.8.19 from the [Arduino download page](https://www.arduino.cc/en/software)
  - [x] On laptop, extract to a suitable location e.g. `~/Applications/arduino-1.8.19/`
  - [x] From inside the folder,  run the install script that creates desktop links:
  
  ```bash
     $ sudo sh install.sh
  ```
  
  - [x] Open the IDE, under **Tools** select **Board:"Arduino Nano"**, **Processor:"ATmega328P (OldBootloader)"** and **Port:"/dev/ttyUSB0"**. Note: choosing the wrong processor gives [this error](https://support.arduino.cc/hc/en-us/articles/4401874331410#avrdude-stk500_recv-and-stk500_getsync)
  
  arduino_setup
  
  - [x] If it still does not connect add the user to the `dialout` group:
  
  ```
  $ ls -l /dev/ttyUSB*
  crw-rw---- 1 root dialout 188, 0 Nov 20 13:47 /dev/ttyUSB0
  $ sudo usermod -a -G dialout <username>
  ```
  
  Tested with **Blink** and **AnalogReadSerial** under **File -> Examples -> 01.Basics** 

### Other tools
- [x] 12V bench power supply
- [ ] Battery charger
- [x] Multimeter
- [x] Soldering iron and solder
- [x] Crimp tools, screwdrivers, Pliers, tieraps, screws,
- [x] rotary tool
- [ ] 3D printer

## (#02) Network setup
Link to blog post: [Getting Ready for ROS Part 2: Networking](https://articulatedrobotics.xyz/ready-for-ros-2-networking/)

Network is needed to remotely control our robot, have robots work together and split computation over multiple machines. ROS provides the protocols, we just need to ensure all computers are in the same network. Requisites:

* Fast reliable connection between robot and laptop
* Internet access to install sfw and back-up in git
* Control over the network e.g. to set up fixed IP addresses

3 options for architecture:

* Existing network: rpi and laptop connected to the router. Easy but not portable, lacks control (DHCP/static IP, network congestion, dropouts etc), may lead to ROS conflicts when using more than one robot
* Access point network: configure laptop to generate wifi network, robot connects to it. Flexible but requires effort to configure, a second wifi card, complex with more than one base computer.
* Dedicated network with a travel router. Preferred.

- [x] Install `ssh` on RPi using keyboard mouse and monitor

```bash
(RPi):$ sudo apt install openssh-server
```

- [x] Get the local IP address of RPi with

```bash
(RPi):$ ip addr
```

- [x] To access RPi terminal remotely from laptop:

```bash
(laptop):$ ssh <pi_username>@<pi_ip_address> # in particular ssh mhered@192.168.8.105

```
- [ ] Write a config file with [`netplan`](https://netplan.io) **Note: my laptop does not have Ethernet port!**

Other tools:

* `scp` for file transfer
* X forwarding to run GUIs remotely
* VS code [remote development extension pack](https://code.visualstudio.com/docs/remote/ssh)

## (#03) Install ROS

Link to blog post: [Getting Ready for ROS Part 3: Installing ROS](https://articulatedrobotics.xyz/ready-for-ros-3-installing-ros/)
Install ROS on both `laptop` and `RPi`:
- [X] Check UTF-8 is set and that the Ubuntu universe repo is enabled with: 
```bash
$ locale
...
$ apt-cache policy | grep universe
```
The second should result in something like:
```
500 http://ports.ubuntu.com/ubuntu-ports focal/universe arm64 Packages
     release v=20.04,o=Ubuntu,a=focal,n=focal,l=Ubuntu,c=universe,b=arm64
```
Note: cfr. the [ROS Foxy installation guide](https://docs.ros.org/en/foxy/Installation/Ubuntu-Install-Debians.html) if more details needed. 
- [X] Add ROS2 apt repo to the system with:
```bash
$ sudo apt update && sudo apt install curl gnupg2 lsb-release
$ sudo curl -sSL https://raw.githubusercontent.com/ros/rosdistro/master/ros.key  -o /usr/share/keyrings/ros-archive-keyring.gpg
$ echo "deb [arch=$(dpkg --print-architecture) signed-by=/usr/share/keyrings/ros-archive-keyring.gpg] http://packages.ros.org/ros2/ubuntu $(source /etc/os-release && echo $UBUNTU_CODENAME) main" | sudo tee /etc/apt/sources.list.d/ros2.list > /dev/null
```
- [X] Install `ros2` and `colcon` and add sourcing of the ROS2 environment to `~/.bashrc` with:
```bash
$ sudo apt update && sudo apt upgrade
$ sudo apt install ros-foxy-desktop
$ sudo apt install python3-colcon-common-extensions
$ echo "source /opt/ros/foxy/setup.bash" >> ~/.bashrc
$ source ~/.bashrc
```

- [X] Test communication between a node written in C++ running on the laptop and a python node running on RPi: 
```bash
(laptop:)$ ros2 run demo_nodes_cpp talker
...
[INFO] [1662750396.990408713] [talker]: Publishing: 'Hello World: 67'
[INFO] [1662750397.990414028] [talker]: Publishing: 'Hello World: 68'
[INFO] [1662750398.990288416] [talker]: Publishing: 'Hello World: 69'
...
```
```bash
(RPi:)$ ros2 run demo_nodes_py listener
...
[INFO] [1662750392.965285945] [listener]: I heard: [Hello World: 63]
[INFO] [1662750393.965151014] [listener]: I heard: [Hello World: 64]
[INFO] [1662750394.965403701] [listener]: I heard: [Hello World: 65]
...
```
Success!

## (#04) 10 concepts about ROS

Link to blog post: [Getting Ready for ROS Part 4: ROS Overview (10 concepts you need to know)](https://articulatedrobotics.xyz/ready-for-ros-4-ros-overview/)

1. ROS Distributions
2. Nodes
3. Topics and Messages
4. Services
5. Node Arguments (Parameters and Remapping)
6. Launch Files
7. Packages
8. System Install (the underlay)
9. Workspaces/Overlays
10. QoS

## (#05) Create a package

Link to blog post: [Getting Ready for ROS Part 5: Making your First Package](https://articulatedrobotics.xyz/ready-for-ros-5-packages/)

1. Create a workspace 
2. Create a package
3. Build it
4. Upload to git
5. Pull from git to the robot
6. Test it

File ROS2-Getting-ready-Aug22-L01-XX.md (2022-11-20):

# Articulated Robotics - Getting Ready for ROS series 

[Getting ready to Build Robots with ROS youtube playlist](https://www.youtube.com/playlist?list=PLunhqkrRNRhYYCaSTVP-qJnyUPkTxJnBt)

8+1 videos covering the setup and an overview of ROS2, TF, URDF and gazebo

## (#01) What we need 

Link to blog post: [Getting Ready for ROS Part 1: What you need](https://articulatedrobotics.xyz/ready-for-ros-1-what-you-need/)

### Skills

Basic Admin: install and configure OS
Move around in Linux
Git for version tracking
Programming & Compiling
Basic electronics: programming an arduino, soldering, connecting a breadboard

### Hardware setup
How to balance small, low energy, powerful and cheap? split computing between 2 paired computers:
* a small onboard computer on the robot (RPi): takes sensor data, sends for processing over network to base station. Receives results and send signals to actuators
* a powerful off-board base station and development machine (mid-range laptop): runs algorithms for processing, takes joystick input, provides visualization and doubles as development machine for coding comfotsably

Docker and virtual machines are fiddly better full Ubuntu installation

### Software
- [x] LTS ROS 2 Foxy Fitzroy is compatible with Ubuntu 20.04 focal fossa (ubuntu mate 64 bits https://ubuntu-mate.org/download). Today latest is ROS 2 Humble and Ubuntu 22.04 Jellyfish.

- [x] version control sfw: git in both rpi and laptop

``` bash
$ sudo apt install git
```
- [x] code editor: vscode only needed on laptop

``` bash
$ sudo snap install --classic code
```
- [x] recommended install also VS code [remote development extension pack](https://code.visualstudio.com/docs/remote/ssh) to code on RPi without a screen

- [x] arduino IDE on both computers ([instructions](https://docs.arduino.cc/software/ide-v1/tutorials/Linux)):
  - [x] Download [ARM Linux 64 bits](https://downloads.arduino.cc/arduino-1.8.19-linuxaarch64.tar.xz) and [Linux 64 bits](https://downloads.arduino.cc/arduino-1.8.19-linux64.tar.xz) versions of IDE 1.8.19 from the [Arduino download page](https://www.arduino.cc/en/software)
  - [x] On laptop, extract to a suitable location e.g. `~/Applications/arduino-1.8.19/`
  - [x] From inside the folder,  run the install script that creates desktop links:
  
  ```bash
     $ sudo sh install.sh
  ```
  
  - [x] Open the IDE, under **Tools** select **Board:"Arduino Nano"**, **Processor:"ATmega328P (OldBootloader)"** and **Port:"/dev/ttyUSB0"**. Note: choosing the wrong processor gives [this error](https://support.arduino.cc/hc/en-us/articles/4401874331410#avrdude-stk500_recv-and-stk500_getsync)
  
  arduino_setup
  
  - [x] If it still does not connect add the user to the `dialout` group:
  
  ```
  $ ls -l /dev/ttyUSB*
  crw-rw---- 1 root dialout 188, 0 Nov 20 13:47 /dev/ttyUSB0
  $ sudo usermod -a -G dialout <username>
  ```
  
  Tested with **Blink** and **AnalogReadSerial** under **File -> Examples -> 01.Basics** 

### Other tools
- [x] 12V bench power supply
- [ ] Battery charger
- [x] Multimeter
- [x] Soldering iron and solder
- [x] Crimp tools, screwdrivers, Pliers, tieraps, screws,
- [x] rotary tool
- [ ] 3D printer

## (#02) Network setup
Link to blog post: [Getting Ready for ROS Part 2: Networking](https://articulatedrobotics.xyz/ready-for-ros-2-networking/)

Network is needed to remotely control our robot, have robots work together and split computation over multiple machines. ROS provides the protocols, we just need to ensure all computers are in the same network. Requisites:

* Fast reliable connection between robot and laptop
* Internet access to install sfw and back-up in git
* Control over the network e.g. to set up fixed IP addresses

3 options for architecture:

* Existing network: rpi and laptop connected to the router. Easy but not portable, lacks control (DHCP/static IP, network congestion, dropouts etc), may lead to ROS conflicts when using more than one robot
* Access point network: configure laptop to generate wifi network, robot connects to it. Flexible but requires effort to configure, a second wifi card, complex with more than one base computer.
* Dedicated network with a travel router. Preferred.

- [x] Install `ssh` on RPi using keyboard mouse and monitor

```bash
(RPi):$ sudo apt install openssh-server
```

- [x] Get the local IP address of RPi with

```bash
(RPi):$ ip addr
```

- [x] To access RPi terminal remotely from laptop:

```bash
(laptop):$ ssh <pi_username>@<pi_ip_address> # in particular ssh mhered@192.168.8.105

```
- [ ] Write a config file with [`netplan`](https://netplan.io) **Note: my laptop does not have Ethernet port!**

Other tools:

* `scp` for file transfer
* X forwarding to run GUIs remotely
* VS code [remote development extension pack](https://code.visualstudio.com/docs/remote/ssh)

## (#03) Install ROS

Link to blog post: [Getting Ready for ROS Part 3: Installing ROS](https://articulatedrobotics.xyz/ready-for-ros-3-installing-ros/)
Install ROS on both `laptop` and `RPi`:
- [X] Check UTF-8 is set and that the Ubuntu universe repo is enabled with: 
```bash
$ locale
...
$ apt-cache policy | grep universe
```
The second should result in something like:
```
500 http://ports.ubuntu.com/ubuntu-ports focal/universe arm64 Packages
     release v=20.04,o=Ubuntu,a=focal,n=focal,l=Ubuntu,c=universe,b=arm64
```
Note: cfr. the [ROS Foxy installation guide](https://docs.ros.org/en/foxy/Installation/Ubuntu-Install-Debians.html) if more details needed. 
- [X] Add ROS2 apt repo to the system with:
```bash
$ sudo apt update && sudo apt install curl gnupg2 lsb-release
$ sudo curl -sSL https://raw.githubusercontent.com/ros/rosdistro/master/ros.key  -o /usr/share/keyrings/ros-archive-keyring.gpg
$ echo "deb [arch=$(dpkg --print-architecture) signed-by=/usr/share/keyrings/ros-archive-keyring.gpg] http://packages.ros.org/ros2/ubuntu $(source /etc/os-release && echo $UBUNTU_CODENAME) main" | sudo tee /etc/apt/sources.list.d/ros2.list > /dev/null
```
- [X] Install `ros2` and `colcon` and add sourcing of the ROS2 environment to `~/.bashrc` with:
```bash
$ sudo apt update && sudo apt upgrade
$ sudo apt install ros-foxy-desktop
$ sudo apt install python3-colcon-common-extensions
$ echo "source /opt/ros/foxy/setup.bash" >> ~/.bashrc
$ source ~/.bashrc
```

- [X] Test communication between a node written in C++ running on the laptop and a python node running on RPi: 
```bash
(laptop:)$ ros2 run demo_nodes_cpp talker
...
[INFO] [1662750396.990408713] [talker]: Publishing: 'Hello World: 67'
[INFO] [1662750397.990414028] [talker]: Publishing: 'Hello World: 68'
[INFO] [1662750398.990288416] [talker]: Publishing: 'Hello World: 69'
...
```
```bash
(RPi:)$ ros2 run demo_nodes_py listener
...
[INFO] [1662750392.965285945] [listener]: I heard: [Hello World: 63]
[INFO] [1662750393.965151014] [listener]: I heard: [Hello World: 64]
[INFO] [1662750394.965403701] [listener]: I heard: [Hello World: 65]
...
```
Success!

## (#04) 10 concepts about ROS

Link to blog post: [Getting Ready for ROS Part 4: ROS Overview (10 concepts you need to know)](https://articulatedrobotics.xyz/ready-for-ros-4-ros-overview/)

1. ROS Distributions
2. Nodes
3. Topics and Messages
4. Services
5. Node Arguments (Parameters and Remapping)
6. Launch Files
7. Packages
8. System Install (the underlay)
9. Workspaces/Overlays
10. QoS

## (#05) Create a package

Link to blog post: [Getting Ready for ROS Part 5: Making your First Package](https://articulatedrobotics.xyz/ready-for-ros-5-packages/)

1. Create a workspace 
2. Create a package
3. Build it
4. Upload to git
5. Pull from git to the robot
6. Test it 

## First prototype (20/11/22)

### Notes

- 12V from bench power source
- A split takes the 12V to the buck converter and the motor driver.
- Buck converter takes 12V at IN+ /IN- and yields 5V at OUT+/OUT- to power the RPi
- RPi takes 5V at pin 4 (5V)/ pin 6(GND) - [How do I power my Raspberry Pi](https://robocraze.com/blogs/post/how-do-i-power-my-raspberry-pi)
- Arduino Nano powered from RPi via USB
- Motor Driver is powered by 12V at 12V/GND pins. 5V jumper is installed, 5V terminal not connected - Could I use this to power the RPi?
- OUT1/OUT2 are connected to the Red/White of the motor. The remaining 4 cables of the encoder are disconnected.
- Connecting the IN1 / IN2 to 5V (e.g. to the 5V pin of the Arduino Nano, cfr. [the Nano pinout in this tutorial](https://diyi0t.com/arduino-nano-tutorial/)) makes the Motor rotate CV / CCV  

### Diagram and overview

prototype_diagram

first_prototype

### Shutting down

First, SSH into the RPi to shut it down:

```bash
(RPi) $ sudo shutdown -h now
```

Then switch off the power supply

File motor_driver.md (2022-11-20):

# L298N Motor driver

 Dimensions: ‎ 5 x 5 x 3 cm

Weight: 27 grams 

Motor output voltage	5V – 35V
Motor output voltage (Recommended)	7V – 12V
Logic input voltage	5V – 7V
Continuous current per channel	2A
Max Power Dissipation	25W

## Tutorials

* [Interface L298N DC Motor Driver Module with Arduino](https://lastminuteengineers.com/l298n-dc-stepper-driver-arduino-tutorial/)

* [L298N Motor Driver – Arduino Interface, How It Works, Codes, Schematics](https://howtomechatronics.com/tutorials/arduino/arduino-dc-motor-control-tutorial-l298n-pwm-h-bridge/)

* [How to use the L298N Motor Driver ](https://create.arduino.cc/projecthub/ryanchan/how-to-use-the-l298n-motor-driver-b124c5)

## Pinout

motor_driver_wiring

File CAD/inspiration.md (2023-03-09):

# Inspiration





Link: https://sketchfab.com/3d-models/futuristic-delivery-bot-9cdd39ab3efa4f9983b150eab70b089d

## First version (8/3/22)



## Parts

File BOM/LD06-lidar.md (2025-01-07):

# LD06 Lidar

Weight: 91g

cfr: https://articulatedrobotics.xyz/mobile-robot-8-lidar/

2D Lidar manufacturer provides a driver that publishes standard ROS messages of type  `sensor_msgs/LaserScan` with the array of measurements and parameters, including the TF where the Lidar is attached so location of measured points in space can be determined.

Similarly 3D Lidar and depth cameras use `sensor_msgs/PointCloud2`

## References

* LD06 small lidar - How to use the Lidar LD06 ROS2: https://www.youtube.com/watch?v=OJWAsV6-0GE

* LDRobot official page: https://www.ldrobot.com/product/en/98

* The download section https://www.ldrobot.com/download/en/98 used to have Datasheet, Development Manual and SDK (Linux, ROS, ROS2) - luckily copied to /assets folder in this repo

* My repo [Minipupper_fun](https://github.com/mhered/minipupper_fun) has information e.g. PC setup [here](https://github.com/mhered/minipupper_fun/blob/main/MiniPupper_SLAM_Navigation.md) and links [here](https://github.com/mhered/minipupper_fun/blob/main/LD06_Links.md)

## Installing LD06 on RPi

1. Clone and symlink the repo:

```bash
(RPi):$ mkdir ~/git && cd ~/git
(RPi):$ git clone https://github.com/ldrobotSensorTeam/ldlidar_stl_ros2
(RPi):$ ln -s ~/git/ldlidar_stl_ros2/ ~/dev_ws/src/
```

2. Plug the LD06 and find out the device id (`by-id` because the path `/dev/ttyUSB*` may change):

```bash
(RPi):$ ls /dev/serial/by-id
usb-1a86_USB2.0-Ser_-if00-port0
usb-Silicon_Labs_CP2102_USB_to_UART_Bridge_Controller_0001-if00-port0
```

Where `usb-Silicon_Labs_CP2102_USB_to_UART_Bridge_Controller_0001-if00-port0` is the LD06 ( and`usb-1a86_USB2.0-Ser_-if00-port0` is the arduino)

3. Set device permissions:

```bash
(RPi):$ sudo chmod 777 /dev/serial/by-id/usb-Silicon_Labs_CP2102_USB_to_UART_Bridge_Controller_0001-if00-port0
```

4. Edit `ldlidar_stl_ros2/launch/ld06.launch.py` to update `port_name` and build the package and source:

```bash 
(RPi):$ colcon build
(RPi):$ cd ~/dev_ws
(RPi):$ source install/setup.bash
```

Execute with:

```bash
(RPi):$ ros2 launch ldlidar_stl_ros2 ld06.launch.py
```

View it from PC with:

```bash
(PC):$ rviz2
```

## To do

- [ ] copy lidar launch file to manolobot_uno package
- [ ] make config file for rviz for camera and lidar

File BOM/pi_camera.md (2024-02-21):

# Cameras in ROS

cfr. https://articulatedrobotics.xyz/mobile-robot-9-camera/

Conversion between field of view and focal length:
$$
fov = 2 atan (sensorwidth/2 focallength)
$$
Image axes: 

x: left to right

y: top to bottom

z: into the page / away from the camera

A driver node talks to the camera hardware and publishes:

* `sensor_msgs/Image` messages with the unprocessed images to topic `/my_camera/image_raw` 
*  `sensor_msgs/CompressedImage` messages with compressed images to topic `/my_camera/image_raw/compressed`

*  `sensor_msgs/CameraInfo` messages with calibration, distortion coefficients needed to interpret the raw image data to topic `/my_camera/camera_info` 

ROS Library `image_transport` provides tools to convert from uncompressed to compressed images. ROS packages `image_proc/image_pipelines` publish topics such as `image_color` or `image_rect` using `camera_info` which are more convenient to to be used by algorithms

All topics in `camera_link_optical` are associated to TF frame which is an empty link used as alias and related to `camera_link` with a rotation `rpy="${-pi/2} 0 ${-pi/2}"`

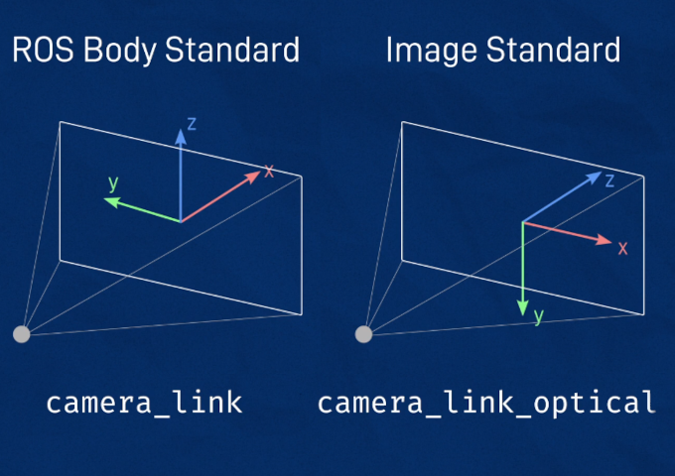
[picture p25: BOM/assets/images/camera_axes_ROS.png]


## Visualizing in RVIZ:

1. Launch RVIZ:

```bash
$ rviz2
```

2. Add **Image** 

3. Select Topic `/camera/image_raw`

Install plugins for image compression to see also `/camera/image/compressed`:

```bash
$ sudo apt install ros-foxy-image-transport-plugins
```

Unfortunately RVIZ does not suport compressed, we need to install also RQT image view:

```bash
$ sudo apt install ros-foxy-rqt-image-view
```

Launch it with:

```bash
$ ros2 run rqt_image_view rqt_image_view
```

## How to republish compressed / raw topic if not implemented in the driver

List existing transports:

```bash
$ ros2 run image_transport list_transports 
Declared transports:
image_transport/compressed
image_transport/compressedDepth
image_transport/raw
image_transport/theora

Details:
----------
"image_transport/compressed"
 - Provided by package: compressed_image_transport
 - Publisher: 
      This plugin publishes a CompressedImage using either JPEG or PNG compression.
    
 - Subscriber: 
      This plugin decompresses a CompressedImage topic.
    
----------
"image_transport/compressedDepth"
 - Provided by package: compressed_depth_image_transport
 - Publisher: 
      This plugin publishes a compressed depth images using PNG compression.
    
 - Subscriber: 
      This plugin decodes a compressed depth images.
    
----------
"image_transport/raw"
 - Provided by package: image_transport
 - Publisher: 
      This is the default publisher. It publishes the Image as-is on the base topic.
    
 - Subscriber: 
      This is the default pass-through subscriber for topics of type sensor_msgs/Image.
    
----------
"image_transport/theora"
 - Provided by package: theora_image_transport
 - Publisher: 
      This plugin publishes a video packet stream encoded using Theora.
    
 - Subscriber: 
      This plugin decodes a video packet stream encoded using Theora.

```

To republish topics from one type to another:

```bash
$ ros2 run image_transport republish compressed raw --ros-args -r in/compresseed:=/camera/image_raw/compressed -r out:=/camera/image_raw/uncompressed

```

```bash
$ ros2 run image_transport republish raw compressed --ros-args -r in:=/camera/image_raw -r out/compressed:=/camera/image_raw/compressed
```

## 

## Setup picamera in Rpi

### First try

Tutorial: https://larrylisky.com/2016/11/24/enabling-raspberry-pi-camera-v2-under-ubuntu-mate/ rather old, from 2016

https://wesleych3n.medium.com/enable-camera-in-raspberry-pi-4-with-64-bit-ubuntu-21-04-d97ce728db9d

Note: Connect ribbon with blue side facing the USB connectors

```bash
(RPi)$ sudo apt-get update
(RPi)$ sudo apt-get upgrade
```

Installation of `raspi-config` failed

```bash
(RPi)$ sudo apt-get install raspi-config rpi-update
Reading package lists... Done
Building dependency tree       
Reading state information... Done
E: Unable to locate package raspi-config
E: Unable to locate package rpi-update
```

On the other hand the file `/boot/firmware/config.txt` already had the lines:

```
start_x=1
gpu_mem=128
```

`/dev/video0/` was detected:

```bash
$ ls -ltrh /dev/video*
crw-rw----+ 1 root video 81, 0 Apr 21  2022 /dev/video13
crw-rw----+ 1 root video 81, 1 Apr 21  2022 /dev/video10
crw-rw----+ 1 root video 81, 2 Apr 21  2022 /dev/video14
crw-rw----+ 1 root video 81, 4 Apr 21  2022 /dev/video16
crw-rw----+ 1 root video 81, 3 Apr 21  2022 /dev/video15
crw-rw----+ 1 root video 81, 7 Apr 21  2022 /dev/video12
crw-rw----+ 1 root video 81, 6 Apr 21  2022 /dev/video0
crw-rw----+ 1 root video 81, 5 Apr 21  2022 /dev/video11

```

And `cheese` was already installed

I tested with `cheese`  (cfr. https://linuxconfig.org/how-to-test-webcam-on-ubuntu-20-04-focal-fossa) and the camera works but is very slow, has low resolution, and weird colors.

This article: https://raspberrypi.stackexchange.com/questions/114035/picamera-and-ubuntu-20-04-arm64 recommends using `opencv` but mentions there is active development to support `libcamera`? in ubuntu arm 64b.

However this guy claims `raspiconfig` can be installed in Ubuntu Mate: https://ubuntu-mate.community/t/install-raspi-config-on-ubuntu-mate-20-10-and-higher/23974

### Second try

Install sfw in Rpi:

```bash
(Rpi):$ sudo apt update
(Rpi):$ sudo apt upgrade
(Rpi):$ sudo apt install libraspberrypi-bin v4l-utils ros-foxy-v4l2-camera
```

Check your user is in the `video` group:

```bash
(Rpi):$ groups
mhered adm dialout cdrom sudo dip video plugdev input lxd lpadmin sambashare spi i2c gpio
```

Otherwise add your user to the `video` group it with:

```bash
(Rpi):$ sudo usermod -aG video mhered
(Rpi):$ reboot
```

Check camera is connected:

```bash
(Rpi):$ vcgencmd get_camera
supported=1 detected=1
```

Stream with:

```bash
(Rpi):$ raspistill -k
```

Quit with `x`

Check if `v4l` (video for linux) can see the camera with:

```bash
(Rpi):$ v4l2-ctl --list-devices
bcm2835-codec-decode (platform:bcm2835-codec):
	/dev/video10
	/dev/video11
	/dev/video12
	/dev/media1

bcm2835-isp (platform:bcm2835-isp):
	/dev/video13
	/dev/video14
	/dev/video15
	/dev/video16
	/dev/media0

mmal service 16.1 (platform:bcm2835-v4l2):
	/dev/video0
```

We install image_transport library and rqt_image_view:

```bash
(Rpi):$ sudo apt install ros-foxy-image-transport-plugins ros-foxy-rqt-image-view
```

Launch driver node:

```bash
(Rpi):$ ros2 run v4l2_camera v4l2_camera_node --ros-args -p image_size:="[640,480]" -p camera_frame_id:=camera_link_optical
```

which is equivalent to the following `camera.launch.py` launch file 

```python
import os

from launch import LaunchDescription
from launch_ros.actions import Node

def generate_launch_description():

    return LaunchDescription([

        Node(
            package='v4l2_camera',
            executable='v4l2_camera_node',
            output='screen',
            parameters=[{
                'image_size': [640,480],
                'camera_frame_id': 'camera_link_optical'
                }]
    )
    ])
```

Note: To run the launch file first we have to pull the changes to the local repo in the robot, make a workspace, symlink the repo and build the package (I had done all this in the PC but not yet in the robot):

```bash
$ mkdir ~/dev_ws && cd ~/dev_ws
$ mkdir src && cd src
ln -s ~/manolobot/manolobot_uno/ ~/dev_ws/src/
$ cd ..
$ colcon build --symlink-install
$ source install/setup.bash
$ ros2 launch manolobot_uno camera.launch.py
```

Then launch `rqt_image_view` from the PC:

```bash
(PC):$ ros2 run rqt_image_view rqt_image_view
```

Note: it broadcasts only over `/image_raw_compressed/`

## Next steps

- [ ] modify camera launch file to also convert compressed to raw images and broadcast them (maybe from PC?)
- [ ] Explore v4l2 repo: https://gitlab.com/boldhearts/ros2_v4l2_camera/-/tree/foxy 
- [ ] Explore: https://medium.com/swlh/raspberry-pi-ros-2-camera-eef8f8b94304 includes ROS2 in Raspbian, v4l2, and tips about going further with opencv and ROS2 tensorflow lite

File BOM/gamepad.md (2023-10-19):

# Game pad setup

This section is largely based in [this article from Articulated Robotics](https://articulatedrobotics.xyz/mobile-robot-14a-teleop/)

I use an old PS4-compatible controller by [BINBOK](https://binbok.com/) (I got it bundled with Minipupper). 8 axes, 13 buttons.

1. Install software (Note: `libcanberra` is to fix the error message `Failed to load module "canberra-gtk-module"` when running `jstest-gtk` see [here](https://raspberryparatorpes.net/dudas/como-arreglar-el-error-gtk-message-failed-to-load-module-canberra-gtk-module/)):

```bash
$ sudo apt update
$ sudo apt upgrade
$ sudo apt install joystick jstest-gtk evtest
$ sudo apt-get install libcanberra-gtk-module libcanberra-gtk0
```

2. Connect controller via USB to charge.
3. Disconnect USB. Press HOME + SHARE until the light flashes White to pair. 
4. Open Bluetooth Settings click on Wireless Controller to Connect. Light turns Blue.

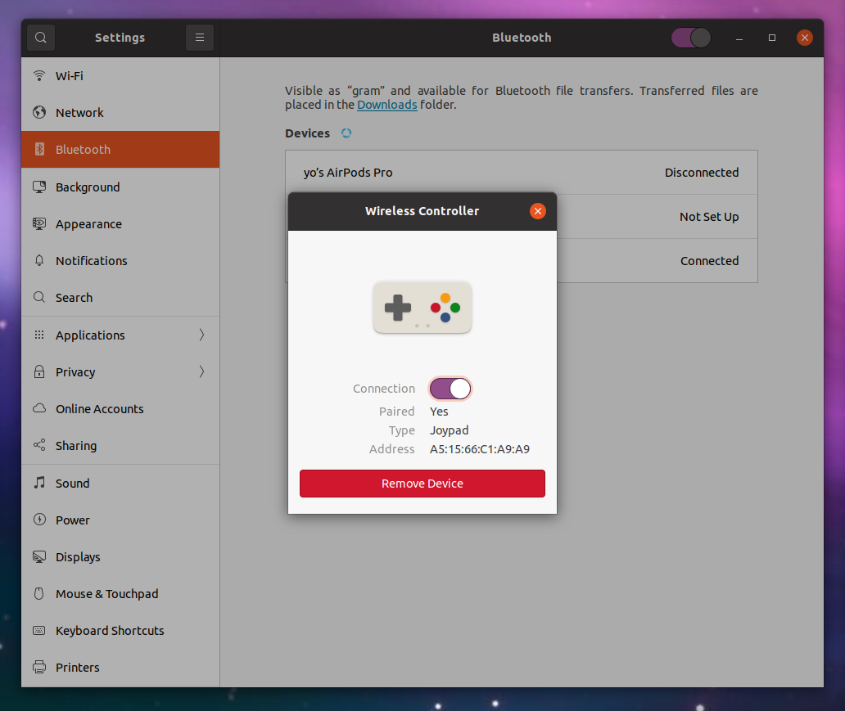
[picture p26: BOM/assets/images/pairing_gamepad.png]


5. Test it works with:

```bash
$ evtest
No device specified, trying to scan all of /dev/input/event*
Not running as root, no devices may be available.
Available devices:
/dev/input/event18:	Wireless Controller
Select the device event number [0-18]: 18
Input driver version is 1.0.1
Input device ID: bus 0x5 vendor 0x54c product 0x5c4 version 0x8100
Input device name: "Wireless Controller"
Supported events:
  Event type 0 (EV_SYN)
  Event type 1 (EV_KEY)
    Event code 304 (BTN_SOUTH)
    Event code 305 (BTN_EAST)
    Event code 307 (BTN_NORTH)
    Event code 308 (BTN_WEST)
    Event code 310 (BTN_TL)
    Event code 311 (BTN_TR)
    Event code 312 (BTN_TL2)
    Event code 313 (BTN_TR2)
    Event code 314 (BTN_SELECT)
    Event code 315 (BTN_START)
    Event code 316 (BTN_MODE)
    Event code 317 (BTN_THUMBL)
    Event code 318 (BTN_THUMBR)
  Event type 3 (EV_ABS)
    Event code 0 (ABS_X)
      Value    128
      Min        0
      Max      255
      Flat      15
    Event code 1 (ABS_Y)
      Value    128
      Min        0
      Max      255
      Flat      15
    Event code 2 (ABS_Z)
      Value      0
      Min        0
      Max      255
      Flat      15
    Event code 3 (ABS_RX)
      Value    128
      Min        0
      Max      255
      Flat      15
    Event code 4 (ABS_RY)
      Value    128
      Min        0
      Max      255
      Flat      15
    Event code 5 (ABS_RZ)
      Value      0
      Min        0
      Max      255
      Flat      15
    Event code 16 (ABS_HAT0X)
      Value      0
      Min       -1
      Max        1
    Event code 17 (ABS_HAT0Y)
      Value      0
      Min       -1
      Max        1
  Event type 4 (EV_MSC)
    Event code 4 (MSC_SCAN)
  Event type 21 (EV_FF)
    Event code 80 (FF_RUMBLE)
    Event code 81 (FF_PERIODIC)
    Event code 88 (FF_SQUARE)
    Event code 89 (FF_TRIANGLE)
    Event code 90 (FF_SINE)
    Event code 96 (FF_GAIN)
Properties:
Testing ... (interrupt to exit)
Event: time 1672950462.408306, type 3 (EV_ABS), code 4 (ABS_RY), value 116
Event: time 1672950462.408306, -------------- SYN_REPORT ------------
Event: time 1672950462.409528, type 3 (EV_ABS), code 4 (ABS_RY), value 113
Event: time 1672950462.409528, -------------- SYN_REPORT ------------
Event: time 1672950462.468288, type 3 (EV_ABS), code 4 (ABS_RY), value 122
Event: time 1672950462.468288, -------------- SYN_REPORT ------------
Event: time 1672950462.493314, type 3 (EV_ABS), code 4 (ABS_RY), value 128
Event: time 1672950462.493314, -------------- SYN_REPORT ------------
Event: time 1672950462.621931, type 3 (EV_ABS), code 1 (ABS_Y), value 118
Event: time 1672950462.621931, -------------- SYN_REPORT ------------
Event: time 1672950462.623186, type 3 (EV_ABS), code 1 (ABS_Y), value 58
....
```

6. Alternatively,`jstest-gtk` provides a nicer GUI for testing which also allows reassigning keys and calibrating, not sure what use it has...

```bash
$ jstest-gtk
```

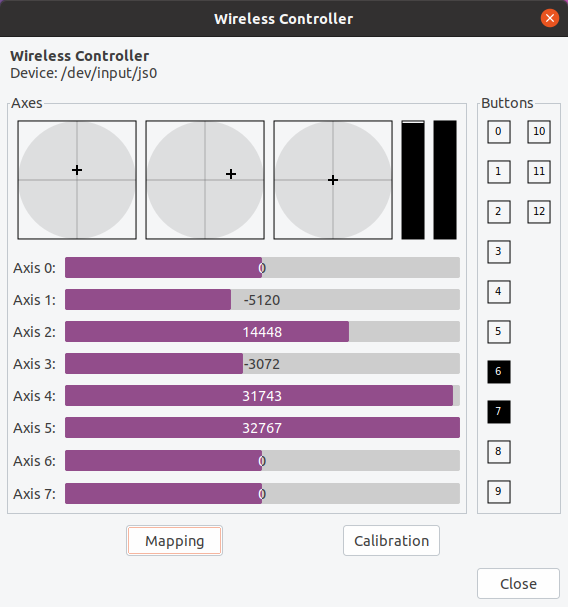
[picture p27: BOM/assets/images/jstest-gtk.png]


Note: The touchpad in the gamepad controls the Mouse

7. To switch off Press HOME button >10s

## Gamepad in ROS

`joy_node` listens to the Linux drivers of the gamepad and publishes `sensor_msgs/Joy` messages

Documentation: https://github.com/ros-drivers/joystick_drivers/tree/ros2/joy

To test it:

```bash
(Terminal 1):$ ros2 run joy joy_enumerate_devices
Joystick Device ID : Joystick Device Name
-----------------------------------------
                 0 : Wireless Controller
(Terminal 1):$ ros2 run joy joy_node
[INFO] [1672951873.296497573] [joy_node]: Opened joystick: Wireless Controller.  deadzone: 0.050000
^C[INFO] [1672952000.449538162] [rclcpp]: signal_handler(signal_value=2)

```

Created `./launch/joystick.launch` - which simply specifies the path to the parameter file, declares a `joy_node` node that uses the params file and launches it. Created also a parameter file `./config/joystick.yaml` with default parameters

After source and build, you can launch the file as follows to achieve the same effect as `ros2 run joy joy_node`:

```bash
$ ros2 launch manolobot_uno joystick.launch.py
```

Then to test it:

```bash
(Terminal 2):$ ros2 topic echo /joy
header:
  stamp:
    sec: 1672951997
    nanosec: 451926026
  frame_id: joy
axes:
- -0.0
- -0.0
- 1.0
- -0.0
- -0.0
- 1.0
- 0.0
- 0.0
buttons:
- 0
- 0
- 0
- 0
- 0
- 0
- 0
- 0
- 0
- 0
- 0
- 0
- 0
---
...
```

List of parametes:

```
/joy_node:
  autorepeat_rate
  coalesce_interval_ms
  deadzone
  device_id
  device_name
  sticky_buttons
  use_sim_time
```

`teleop-twist-joy` listens to raw joystick commands on `/joy`  topic and translates them into `Twist` messages

```
$ sudo apt-get install ros-foxy-teleop-twist-joy
```

Added to `./launch/joystick.launch` the declaration and launch of a `teleop_node` with the same parameter file  `./config/joystick.yaml` which defines the controls: 

- Dead man switches: L button (left shoulder) for normal speed, R button (right shoulder) for turbo
- Control on left stick: vertical axis for forward/backward motion and horizontal axis for rotation.

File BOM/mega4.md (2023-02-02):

# UUGEAR MEGA4 - 4-Port USB Hub

The UUGear MEGA4 is a 4-Port USB 3.1 PPPS (Per-Port Power Switching) hub designed for theRPi

adds 4 USB 3.1 ports

power on each USB port can be individually turned on/off  via software or via UUGear Web Interface (UWI) on PC, Tablet or Smartphone. This allows resetting devices or saving energy (e.g. the Lidar)

can be externally powered connecting a 5V power supply to its  USB-C connector to increase its current output ability up to 5A, and 2.5A per port

there is a protection to prevent the hub from back-powering the RPi.

## Install software

The software is needed to turn on/off the power on each USB port.

Download and run the installation script to install the software in `mega4` directory and the UUGear Web Interface (UWI) in `uwi` directory in the RPi:

```bash
(RPi):$ wget https://www.uugear.com/repo/MEGA4/install.sh
(RPi):$ sudo sh install.sh
```

Note: `sudo` is needed to run the script because it attempts to disable USB auto-suspend in `/boot/cmdline.txt`.

After installing the software, reboot the RPi so the UWI server will run in the background. 

With the default  configuration you should be able to access the MEGA4 via UWI on address https://raspberrypi:8000/mega4/ (Note:???)

## Specs

* Dimensions: 85 x 56 x 9 mm (USB plug protrudes 7mm)

* Weight: 60g (29g without accesories)

* Output Current

  - Bus-powered only: up to 1.2A in total (limited by Raspberry Pi 4B)

  - With supplemental power supply: up to 5A in total, and 2.5A per port (also depends on the power supply)

## References

https://www.uugear.com/product/mega4-4-port-usb-3-ppps-hub-for-raspberry-pi-4b/

https://thepihut.com/products/mega4-4-port-usb-3-1-ppps-hub-for-raspberry-pi-4

https://www.uugear.com/doc/MEGA4_UserManual.pdf

The software is a wrapper of utility uhubctl: https://github.com/mvp/uhubctl

## First try to switch off Lidar

1. install `uhubctl`:

```bashç
(RPi):$ sudo apt install uhubctl
```

2. find devices:

```bash
(RPi):$ sudo uhubctl
Current status for hub 2-2 [2109:0817 VIA Labs, Inc. USB3.0 Hub, USB 3.10, 4 ports]
  Port 1: 02a0 power 5gbps Rx.Detect
  Port 2: 02a0 power 5gbps Rx.Detect
  Port 3: 02a0 power 5gbps Rx.Detect
  Port 4: 02a0 power 5gbps Rx.Detect
Current status for hub 2 [1d6b:0003 Linux 5.4.0-1079-raspi xhci-hcd xHCI Host Controller 0000:01:00.0, USB 3.00, 4 ports]
  Port 1: 02a0 power 5gbps Rx.Detect
  Port 2: 0263 power 5gbps U3 enable connect [2109:0817 VIA Labs, Inc. USB3.0 Hub, USB 3.10, 4 ports]
  Port 3: 02a0 power 5gbps Rx.Detect
  Port 4: 02a0 power 5gbps Rx.Detect
Current status for hub 1-1.2 [2109:2817 VIA Labs, Inc. USB2.0 Hub, USB 2.10, 4 ports]
  Port 1: 0103 power enable connect [0eef:0005 WaveShare ws170120 WaveShare ws170120]
  Port 2: 0103 power enable connect [10c4:ea60 Silicon Labs CP2102 USB to UART Bridge Controller 0001]
  Port 3: 0103 power enable connect [1a86:7523 USB2.0-Ser!]
  Port 4: 0100 power
Current status for hub 1 [1d6b:0002 Linux 5.4.0-1079-raspi xhci-hcd xHCI Host Controller 0000:01:00.0]
  Port 1: 0503 power highspeed enable connect [2109:3431 USB2.0 Hub, USB 2.10, 4 ports]
```

3. switch off (but does not seem to work):

```bash
(RPi):$ sudo uhubctl -a off -l 1-1.2 -p 2
Current status for hub 1-1.2 [2109:2817 VIA Labs, Inc. USB2.0 Hub, USB 2.10, 4 ports]
  Port 2: 0103 power enable connect [10c4:ea60 Silicon Labs CP2102 USB to UART Bridge Controller 0001]
Sent power off request
New status for hub 1-1.2 [2109:2817 VIA Labs, Inc. USB2.0 Hub, USB 2.10, 4 ports]
  Port 2: 0000 off
```

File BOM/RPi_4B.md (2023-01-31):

# Raspberry Pi 4B

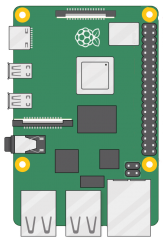
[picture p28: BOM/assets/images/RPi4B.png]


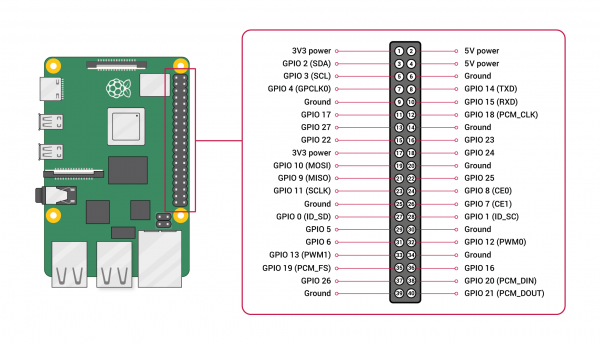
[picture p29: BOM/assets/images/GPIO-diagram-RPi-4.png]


## Soft reset / soft power down button

1. install `pip` in the RPi and then install the [RPi.GPIO](https://pypi.org/project/RPi.GPIO/) package. **Note: with `sudo` so later it will be accessible by `root`  and the python script will run from `/etc/rc.local`**:

```bash
(Rpi):$ sudo apt install python3-pip
(Rpi):$ sudo pip install RPi.GPIO
```

2. To avoid [this error](https://raspberrypi.stackexchange.com/questions/40105/access-gpio-pins-without-root-no-access-to-dev-mem-try-running-as-root), add the user to the `gpio` group and check that the device file `/dev/gpiomem` has the correct permissions:

```bash
(RPi):$ sudo adduser mhered gpio
(Rpi):$ ls -l /dev/gpiomem
crw-rw---- 1 root gpio 244, 0 Dec 28 22:51 /dev/gpiomem
```

	If it doesn't, then set the correct permissions as follows

```bash
(Rpi):$ sudo chown root.gpio /dev/gpiomem
(Rpi):$ sudo chmod g+rw /dev/gpiomem
```

	This needs to be repeated after every reboot so we will add these commands to the end of `/etc/rc.local` 

3. Wire the button to pins 9 (GND) and 11 (GPIO17 - INPUT). Note that the input pin is pulled HIGH by default so pushing it yields LOW.

4. Write the python script that listens for the button: [../code/button/safe_shutdown.py](../code/button/safe_shutdown.py)

	For more details on wiring and the script refer to:

* https://www.electroniclinic.com/how-to-reset-or-shutdown-raspberry-pi-using-a-button/

* https://learn.sparkfun.com/tutorials/raspberry-pi-safe-reboot-and-shutdown-button/all
* https://www.ridgesolutions.ie/index.php/2013/02/22/raspberry-pi-restart-shutdown-your-pi-from-python-code/
* https://raspberrypi.stackexchange.com/questions/69194/using-gpiozero-button-for-2-functions-long-short-press

5. Create `/etc/rc.local`:

```bash
#!/bin/sh -e
#
# File /etc/rc.local
# created by MH on 28.01.2023
#
# This script is executed at the end of each multiuser runlevel.
# Ensure that the script will "exit 0" on success or any other
# value on error.
#
# To enable or disable this script, just change the execution
# bits.
#
# By default, this script does nothing.

# Set permissions for dev/gpiomem
chown root.gpio /dev/gpiomem
chmod g+rw /dev/gpiomem

# run in the background the script that listens for the safe reset/shutdown button
/usr/bin/python3 /home/mhered/manolobot/code/button/safe_shutdown.py &

exit 0
```

5. Give it execution permission:

```bash
(Rpi):$ sudo chmod +x /etc/rc.local
```

Sources on playing with `/etc/rc.local`:

* https://learn.sparkfun.com/tutorials/how-to-run-a-raspberry-pi-program-on-startup 
* https://linuxhint.com/use-etc-rc-local-boot/

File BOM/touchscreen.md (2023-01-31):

# 5inch HDMI LCD (B) Waveshare

## Setup in RPi running Ubuntu Mate

Note the [official wiki](https://www.waveshare.com/wiki/5inch_HDMI_LCD_(B)?Amazon ) refers to Raspbian and there are minor changes in Ubuntu Mate

RPi does not detect automatically the screen configuration, need to add the values to a configuration file:

```bash
(RPi)$ sudo nano /boot/firmware/usercfg.txt
```

Add this section at the end of the file and save:

```
# Waveshare HDMI touchscreen configuration added by MH 21.11
hdmi_group=2
hdmi_mode=87
hdmi_cvt 800 480 60 6 0 0 0
hdmi_drive=1
```

Reboot with `$ sudo reboot`

## Screen calibration

Install calibration software:

```bash
(RPi)$ sudo apt-get install xinput-calibrator
(RPi)$ sudo apt-get install xserver-xorg-input-evdev
(RPi)$ sudo cp -rf /usr/share/X11/xorg.conf.d/10-evdev.conf /usr/share/X11/xorg.conf.d/45-evdev.conf
(RPi)$ sudo reboot
```

This will add a new option in the menu **System Settings -> Administration -> Calibrate Touchscreen**. 

Follow the instructions to calibrate the screen with the stylus. At the end of the process the following message is shown:   
```
Calibrating EVDEV driver for "WaveShare ws170120" id=6
	current calibration values (from XInput): min_x=135, max_x=3925 and min_y=333, max_y=3913

Doing dynamic recalibration:
	Setting calibration data: 129, 3929, 310, 3925
	--> Making the calibration permanent <--
  copy the snippet below into '/etc/X11/xorg.conf.d/99-calibration.conf' (/usr/share/X11/xorg.conf.d/ in some distro's)
Section "InputClass"
	Identifier	"calibration"
	MatchProduct	"WaveShare ws170120"
	Option	"Calibration"	"129 3929 310 3925"
	Option	"SwapAxes"	"0"
EndSection
```
To make the settings permanent create a new config file: 
```bash
(RPi)$ sudo nano /usr/share/X11/xorg.conf.d/99-calibration.conf
```
Paste this section to the file and save it. Note the values will be unique for each device and setup.
```
Section "InputClass"
	Identifier	"calibration"
	MatchProduct	"WaveShare ws170120"
	Option	"Calibration"	"135 3925 333 3913"
	Option	"SwapAxes"	"0"
EndSection
```

Reboot with `$ sudo reboot`

## Flip screen

To flip the screen run:

```bash
(RPi):$ DISPLAY=:0 xrandr --output HDMI-1 --rotate inverted
```

This only works if you are already logged in in the robot GUI, otherwise it throws an error `Invalid MIT-MAGIC-COOKIE-1 key` therefore I enabled autologin (cfr. https://techpiezo.com/linux/enable-or-disable-automatic-login-in-ubuntu-20-04/):

1. The display manager is `lightdm` (to find out, run `(RPI):$ systemctl status display-manager`)

2. Edit the config file with `(RPi):$ sudo nano /etc/lightdm/lightdm.conf` and append:

```
[Seat:*]
autologin-user=mhered
autologin-user-timeout=0
```

3. reboot

To flip also the touch input:

```bash
(RPi):$ DISPLAY=:0 xinput set-prop "WaveShare ws170120" --type=float "Coordinate Transformation Matrix" -1 0 1 0 -1 1 0 0 1
```

To run both automatically at startup run `(RPi):$ sudo nano /etc/xdg/autostart/setscreen.desktop`  and add the following lines:

```
[Desktop Entry]
Name=Set Screen Rotation
Exec=/bin/bash -c 'sleep 10 && xrandr -o inverted && xinput set-prop "WaveShare ws170120" --type=float "Coordinate Transformation Matrix" -1 0 1 0 -1 1 0 0 1'
Type=Application
```

This waits 10s after login, then executes.

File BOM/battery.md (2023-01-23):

# HRB LiPo Battery 

## Battery specs

Capacity: 5000mAh 

Voltage: 11.1V 3S 

Discharge rate: 50C 

XT60 Connector with 4 adapter parts. 

Balance connector: JST-XH

Carbon fibre rigid case: 155×44×24mm (0 - 3mm Unterschied) 

Weight 376 g

Safe charging rate: 0.5-1C (i.e. in my case 5A)

## Rationale for the choice of battery

cfr: https://articulatedrobotics.xyz/mobile-robot-5-power-theory/

### Requirements

#### Consumers @5V:

* RPi 1.5A
* Arduino 0.1A
* Lidar 1A
* PiCamera 0.1A
* Motor driver  0.1A
* LCD 1A

Total: 3.8A @5V --> 1.6A@12V --> 2A 

#### Consumers @12V

2 motors x1.5A = 3A

#### Total requirement

5A @12V during 40'

### Explanation of the specs

#### S-number

e.g. 2S 3S 4S is the number of 3,7V cells in series

3.7 is the storage level, fully charged each cell is 4.2V

e.g. in our case:**NEED 3 (11.1V avg)** 

#### Capacity in mAh

The maximum continuous current in mA that fully discharges the battery over 1h. 

Measures the run time from a single charge, but in practice one should use maximum 2/3 of the charge.

Therefore minutes to safe discharge @5A = CAPACITY mAh/ (5A * 1000mA/A) * 60min(h) *2/3 = 0.008 * CAPACITY

i.e. in our case to achieve approx 40' usable time @5A: **NEED 5000mAh** 

#### C-number

The discharge rate is how fast you can discharge the battery without harming it. 

C-number is the maximum current expressed as a multiplier of the capacity. Typically two values: continuous and burst.

e.g. in our case **50C** * 5000mAH *1A/1000mA= 250A **(more than enough!)** 

## Battery basics

cfr : [Battery basics](https://www.youtube.com/watch?v=4bzyvmiFTZo), [LiPo guide for beginners](https://www.youtube.com/watch?v=Lk7wzVYmXSA)

### Pros/Cons LiPo vs NiCad, NiMH etc

Pros: Lighter, higher capacity, high discharge, various sizes

Cons: Shorter life (100-200 cycles), risk of fire

### Safety

* Never use a puffed or damaged battery
* Never leave a charging battery unattended. Never leave a battery plugged in (either in the robot or in the charger)

* Never charge any cell above 4.2V or below 3.0V

* Never leave a Lipo batttery fully charged or fully dischared more than 3 days: charge them to storage level (3.7V per cell)
* Never immediately use or charge a warm LiPo battery
* Never store batteries in a hot environment. Heat kills batteries.

### Charging

See [How to charge lithium batteries](https://www.makeuseof.com/how-to-charge-a-lipo-battery/ ) for the charger I bought.

Recommended to charge slowly (at 1C)

4 settings: Charge, Balance, Storage, Discharge

* **Charge** may lead one individual cell to overcharge
* Use **Balance** to increase the life, uses **balance connector** to ensure all cells are charged evenly (). Different connectors for 2S, 3S 4S cells. 

* Use **Storage** to charge to 3.7V per cell if you wont use the batteries for months

### Storage

Store in a tin box or lipo pouches

### Connectors

XT60 connector is better than older T or Dean's style connector

Balance connector: to ensure all cells are charged equally. Different connectors for 2S, 3S 4S cells

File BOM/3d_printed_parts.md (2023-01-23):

## PiCamera holder

| Units | CAD file | Color | Material | Source |
| ----- | --- | ----- | --- | --- |
|1 | [picam_A.stl](./assets/CAD/picam_A.stl) | white | ABS | https://www.thingiverse.com/thing:3411450|
|2 | [picam_B_r2.stl](./assets/CAD/picam_B_r2.stl) | white | ABS |  |
|1 |  [picam_C.stl](./assets/CAD/picam_C.stl)  | white | ABS |  |

## Lidar support

| Units | CAD file | Color | Material | Source |
| ----- | --- | ----- | --- | --- |
|1 |  [lidar.stl](./assets/CAD/lidar.stl) | black | PETG | https://www.thingiverse.com/thing:5374323|

## GoPro stand

| Units | CAD file | Color | Material | Source |
| ----- | --- | ----- | --- | --- |
|1 |  [micro_Apex_gopro.stl](./assets/CAD/micro_Apex_gopro.stl) | black | PETG | https://www.thingiverse.com/thing:4890862|

## PiCamera holder with GoPro adapter

| Units | CAD file | Color | Material | Source |
| ----- | --- | ----- | --- | --- |
|1 | [JS_RPi3B__Pos-001_drzak_kamery.stl](./assets/CAD/JS_RPi3B__Pos-001_drzak_kamery.stl)  | black | PETG | https://www.thingiverse.com/thing:3610624|
|1 | [JS_RPi3B__Pos-002_drzak_kamery_zada.stl](./assets/CAD/JS_RPi3B__Pos-002_drzak_kamery_zada.stl)  | black | PETG |  |
|1 | [JS_RPi3B__Pos-003_drzak-adapter_GoPro.stl](./assets/CAD/JS_RPi3B__Pos-003_drzak-adapter_GoPro.stl) |black | PETG |  |
|6 | [JS_RPi3B__Pos-004_podlozka_sroubku_M2.stl](./assets/CAD/JS_RPi3B__Pos-004_podlozka_sroubku_M2.stl)  | black | PETG |  |

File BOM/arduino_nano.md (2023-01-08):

# Arduino Nano

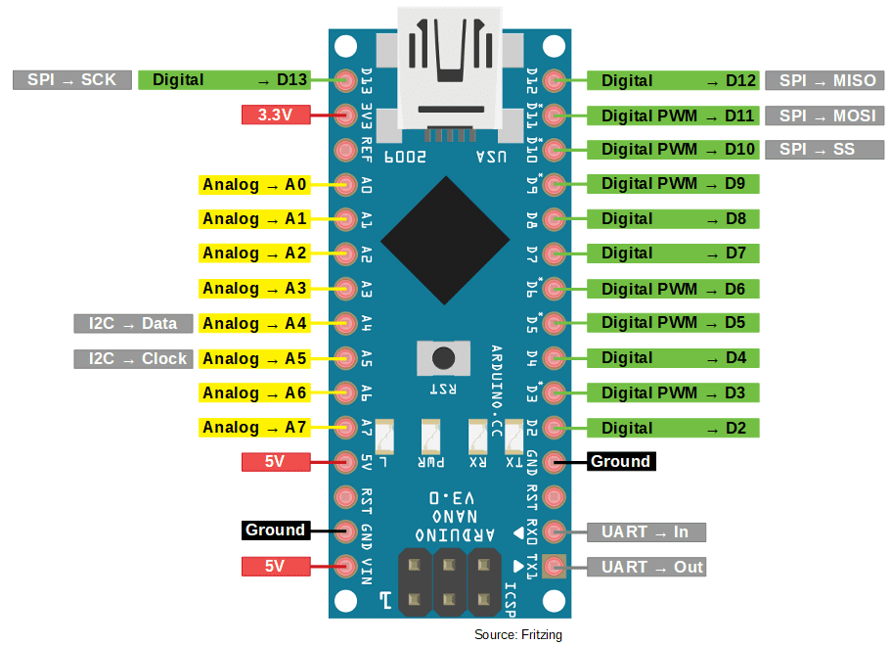
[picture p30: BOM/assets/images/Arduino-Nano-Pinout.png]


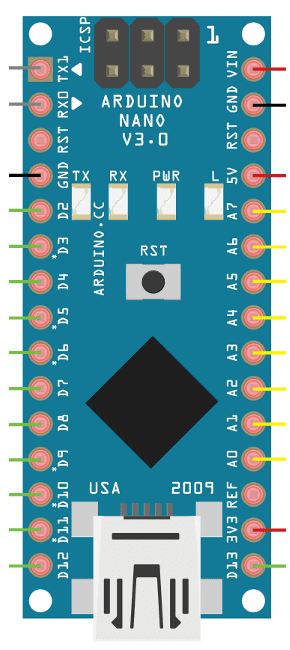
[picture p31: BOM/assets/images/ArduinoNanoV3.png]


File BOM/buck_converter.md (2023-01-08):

# 35W Buck-Boost DC Converter

ARCELI Buck-Boost Converter with display

DC 5.5-30V to DC 0.5-30V  35W

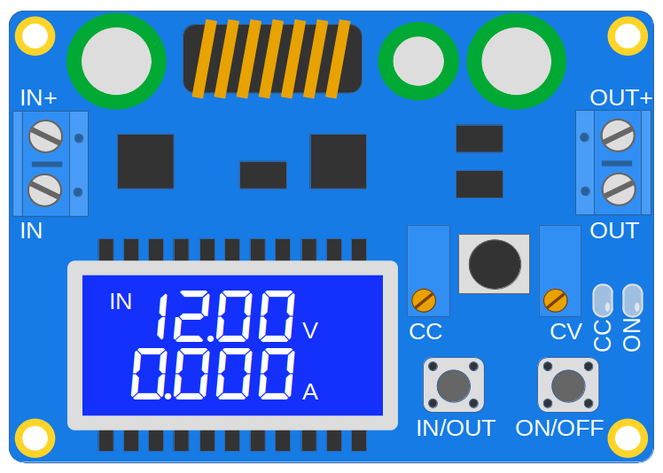
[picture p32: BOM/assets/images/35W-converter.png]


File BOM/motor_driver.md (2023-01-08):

# L298N Motor driver

 Dimensions: ‎ 5 x 5 x 3 cm

Weight: 27 grams 

Motor output voltage	5V – 35V
Motor output voltage (Recommended)	7V – 12V
Logic input voltage	5V – 7V
Continuous current per channel	2A
Max Power Dissipation	25W

## Tutorials

* [Interface L298N DC Motor Driver Module with Arduino](https://lastminuteengineers.com/l298n-dc-stepper-driver-arduino-tutorial/)

* [L298N Motor Driver – Arduino Interface, How It Works, Codes, Schematics](https://howtomechatronics.com/tutorials/arduino/arduino-dc-motor-control-tutorial-l298n-pwm-h-bridge/)

* [How to use the L298N Motor Driver ](https://create.arduino.cc/projecthub/ryanchan/how-to-use-the-l298n-motor-driver-b124c5)

## Pinout

motor_driver_wiring

motor_driver_wiring

motor_driver_wiring

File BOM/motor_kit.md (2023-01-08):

# JGA25-371 Encoder Gear Motor Kit with Mounting Bracket and Wheel

## Contents:

* 1 x JGA25-371 Encoder Gear Motor
* 1 x 65mm Diameter Rubber Tire
* 1 x Brass Coupling
* 1 x Aluminum Alloy Mounting Bracket
* 1 x Motor Cable (14.2cm)
* 1 Set of Screws



## Wheel

Diameter: 65MM 

Thickness: about 27MM

Weight: 35 grams 

Features: 

Rubber tire with a sponge liner

Nylon wheel hub for hex coupling

Tire tread pattern: imitation HPI drift pattern load capacity grip

wheel

## Mounting bracket

Bracket

## Brass coupling

Coupling

## Motor

motor

motor2

[Link to Datasheet](https://www.openimpulse.com/blog/wp-content/uploads/wpsc/downloadables/JGA25-371-data-sheet1.jpg)

JGA25-371-data-sheet1

Datasheet not to be trusted. Measured Stall Current: ca. 1.5A

### Wiring

https://forum.arduino.cc/t/connecting-a-dc-motor-w-encoder-to-arduino-shield/517262/8

connections

Review!!

- Red: motor power + (can be reversed with Red to move motor forward and reverse)
- Black: encoder power - (Voltage range 3.3-5V. Positive and negative can not be connected incorrectly)
- Yellow: Encoder A phase signal feedback (11 signals per turn of the motor)
- Green: Encoder B phase signal feedback (11 signals per turn of the motor)
- Blue: encoder power supply + (Voltage range 3.3-5V. Positive and negative can not be connected incorrectly)
- White: motor power - (can be reversed with Red to move motor forward and reverse) 

## Sources

* [Ebay](https://www.ebay.com/itm/165266268040?hash=item267aa31f88:g:nDMAAOSw7e9dMYIL)
* [Daraz](https://www.daraz.lk/products/jga25-371-smart-car-robot-diy-encoder-gear-motor-with-mounting-bracket-wheel-kit-i109232382.html)
* [Walmart](https://www.walmart.com/ip/Smart-Car-Kit-Small-Size-JGA25-371-Wear-resistant-For-Printers-For-Smart-Cars-For-Robots/1531668648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)
* [AliExpress](https://es.aliexpress.com/item/1005003707407732.html?gatewayAdapt=glo2esp)
* [Amazon](https://www.amazon.es/dp/B07WT22RNK?psc=1&ref=ppx_pop_dt_b_product_details)
* [Openimpulse](https://www.openimpulse.com/blog/products-page/25d-gearmotors/jga25-371-dc-gearmotor-encoder-126-rpm-12-v-2/): motor only, datasheet
* [Plexishop](https://www.plexishop.it/en/robotics-and-automation/motors-for-arduino/dc-motors/jga25-371-geared-motor-with-encoder-126rpm.html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)

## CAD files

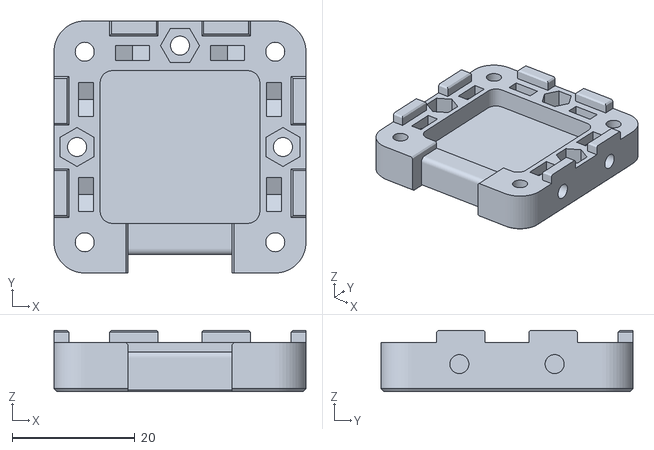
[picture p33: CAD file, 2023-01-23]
BOM/assets/CAD/JS_RPi3B__Pos-002_drzak_kamery_zada.stl
41.0 x 41.0 x 10.0

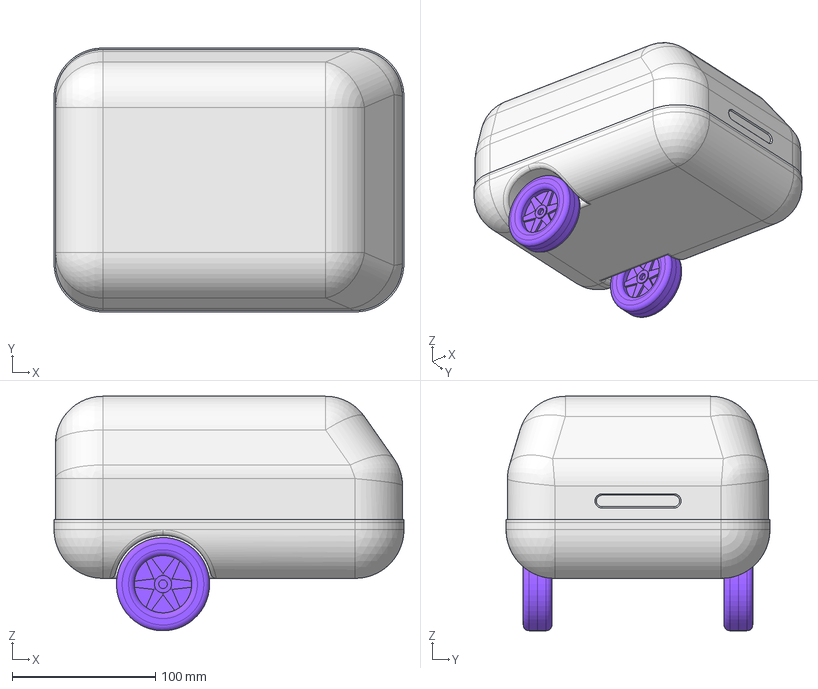
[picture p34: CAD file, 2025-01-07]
CAD/assets/CAD/bot_3.FCStd
244.0 x 184.0 x 163.5 mm
Wheel
Wheel001
Cap
Base_Groove

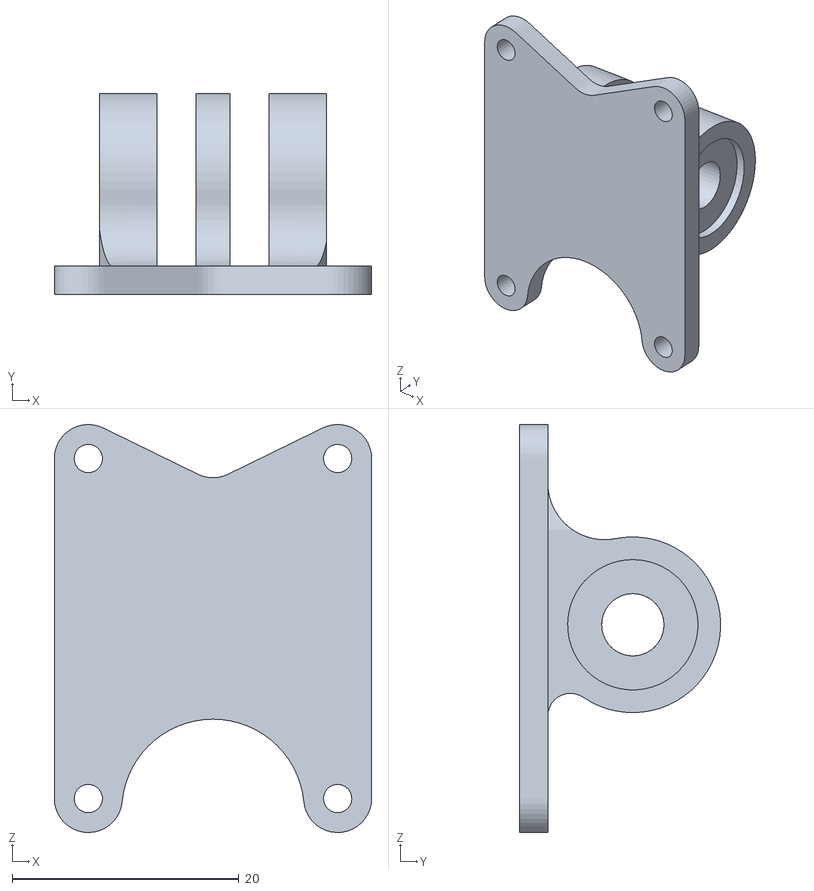
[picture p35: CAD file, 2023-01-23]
BOM/assets/CAD/micro_Apex_gopro.stl
28.0 x 17.7 x 36.0

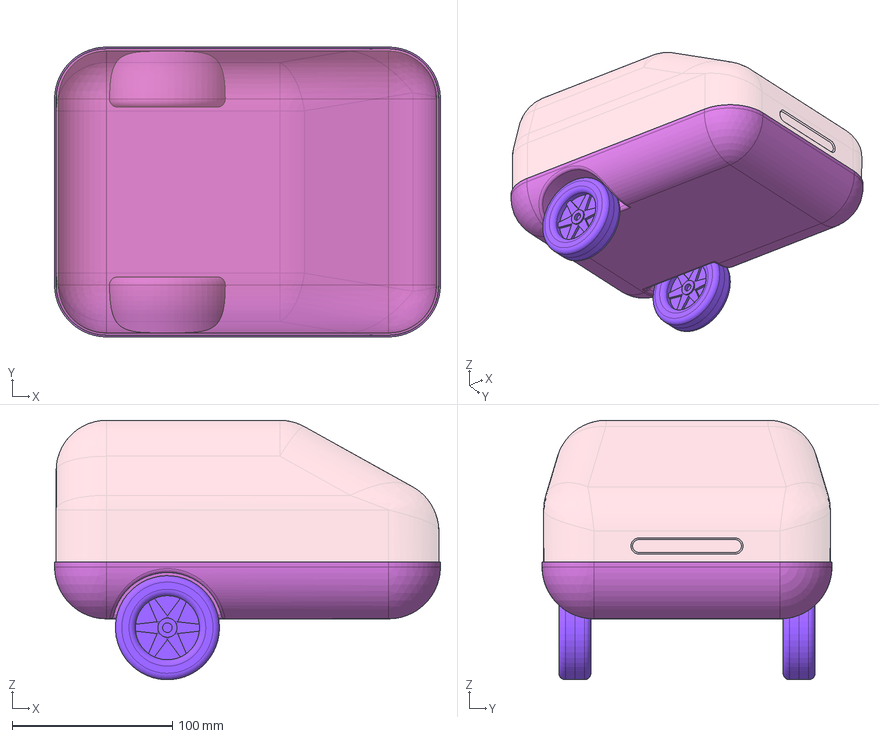
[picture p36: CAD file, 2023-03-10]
CAD/assets/CAD/bot_2.FCStd
241.0 x 181.0 x 162.0 mm
Cap
Base_Groove
Wheel
Wheel001

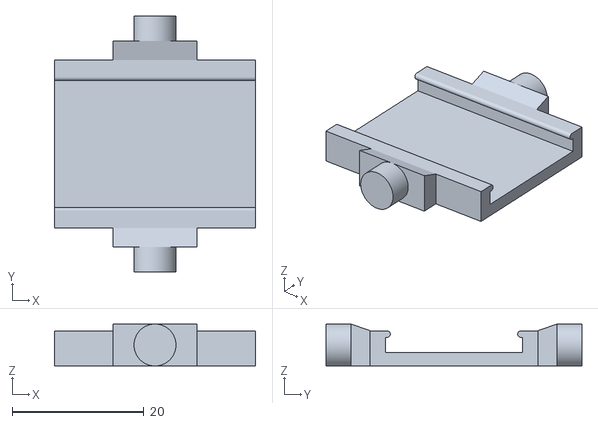
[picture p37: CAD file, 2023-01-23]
BOM/assets/CAD/picam_C.STL
30.5 x 38.8 x 6.35

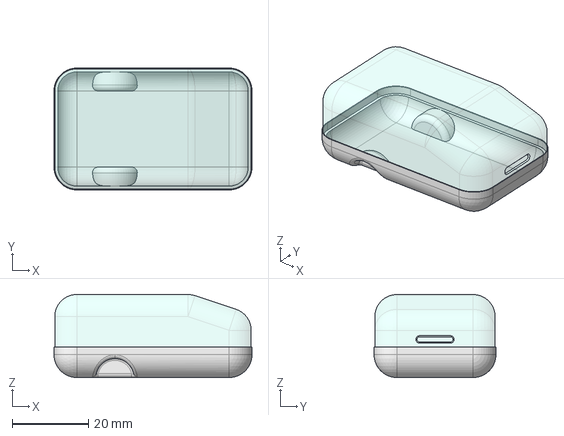
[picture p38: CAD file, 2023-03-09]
CAD/assets/CAD/bot_1.FCStd
52.0 x 32.0 x 21.8 mm
Cap
Base_Groove

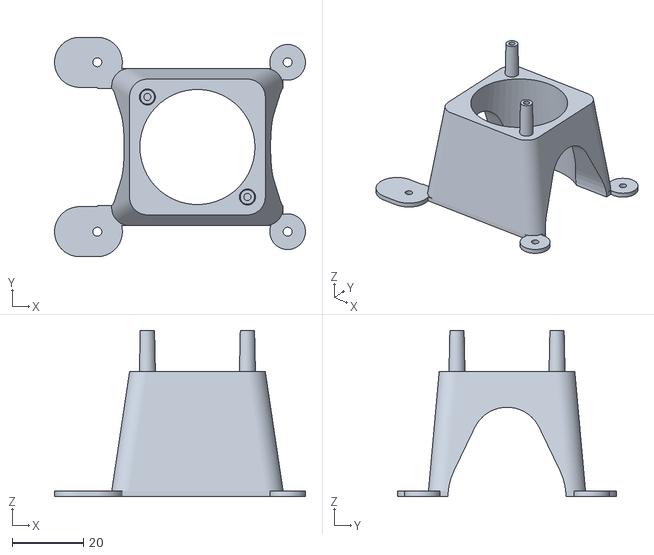
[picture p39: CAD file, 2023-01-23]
BOM/assets/CAD/lidar.stl
70.2 x 61.4 x 46.5

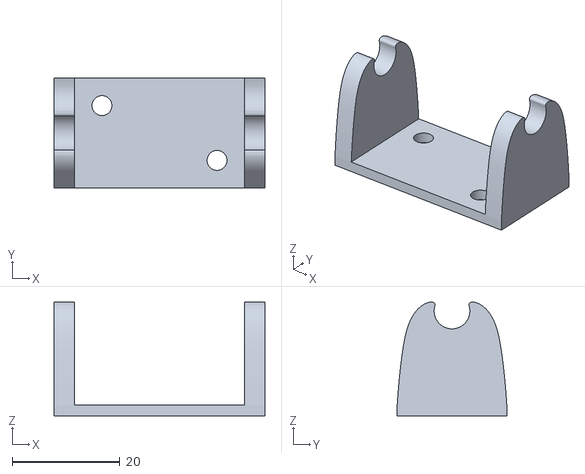
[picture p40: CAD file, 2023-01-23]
BOM/assets/CAD/picam_B_r2.STL
39.1 x 20.3 x 21.1

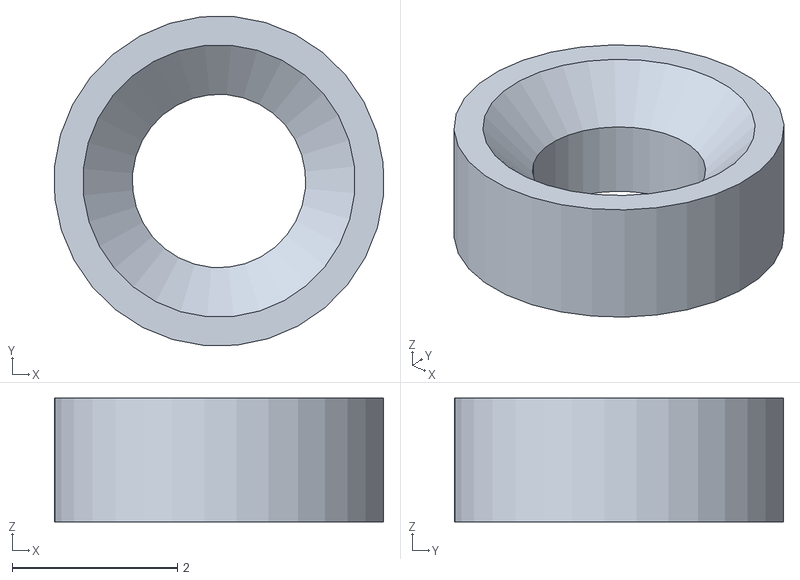
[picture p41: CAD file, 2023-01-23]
BOM/assets/CAD/JS_RPi3B__Pos-004_podlozka_sroubku_M2.stl
3.98 x 3.98 x 1.50

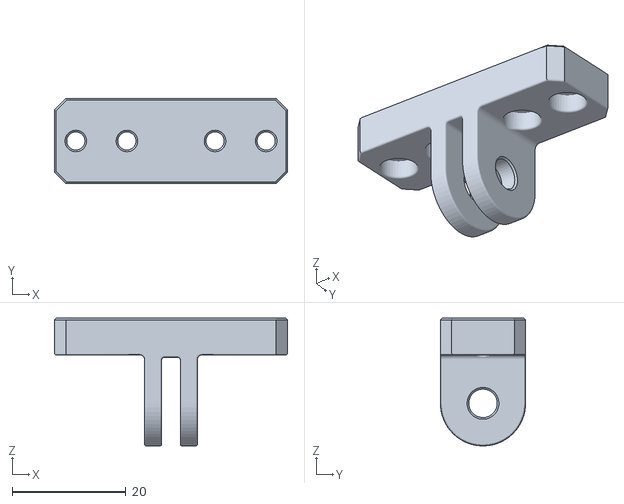
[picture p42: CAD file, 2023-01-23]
BOM/assets/CAD/JS_RPi3B__Pos-003_drzak-adapter_GoPro.stl
41.0 x 15.0 x 22.5

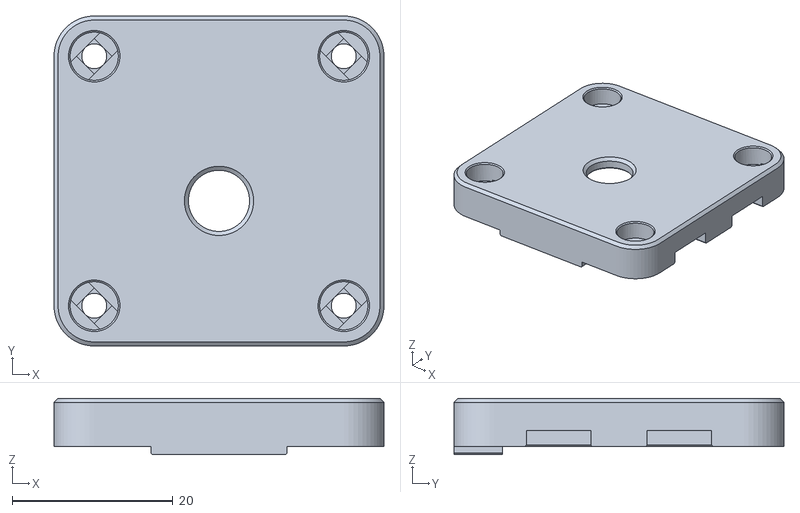
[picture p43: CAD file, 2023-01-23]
BOM/assets/CAD/JS_RPi3B__Pos-001_drzak_kamery.stl
41.0 x 41.0 x 7.00

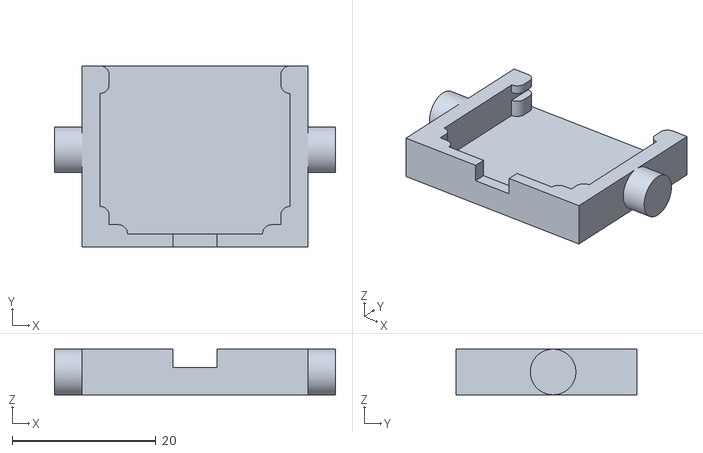
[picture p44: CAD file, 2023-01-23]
BOM/assets/CAD/picam_A.STL
39.1 x 25.2 x 6.36

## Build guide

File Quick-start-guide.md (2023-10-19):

# Quick Start Guide

## Start manubot

### Charge the battery

Balance charging the LiPo battery using the iMAX B6AC LiPo balance charger:

1.  Plug the charger to mains to power it up
2. Check that the jacks of the charging cable are correctly connected to the charger (black to negative and red to positive). 
3.  Connect the XT60 connector of the battery to the charging cable. 
4.  Insert the JST-XH balance connector of the battery to the designated slot in the balance charger (In our case 3 cells). 
5.  Use arrows to go to the **Balance Charge** setting.
6.  Select **LiPo** battery type. 
7. Confirm settings. For the 5000mAh 11.1V 50C LiPo battery: **Lipo**,  **3.8A** charging current (below 1C) and **11.1V (3S)** configuration. 
8.  Hold the **Start** button to start. Press it again to confirm. 
9. During charging: in the screen with 6 voltages it is normal to see the lower three indications static at 0.00. This is because the charger is capable of charging batteries with up to 6 cells, but our battery actually has only three.
10. The charger alarm will beep when charge is complete

### Switch on the robot

Red switch on the side from **O** to **I**

### Source ROS2 in the robot

SSH into the robot and source ROS2 workspace:

```bash
(PC T1)$ ssh mhered@manubot
mhered@192.168.8.105's password: 
...
(manubot T1)$ cd ~/dev_ws/
(manubot T1)$ source install/setup.bash
```

### Spawn the robot

```bash
(manubot T1)$ ros2 launch manolobot_uno launch_robot.launch.py
```

### Source ROS2 in the PC

Source ROS2 workspace in PC:

```bash
(PC T2)$ cd ~/dev_ws/
(PC T2)$ source install/setup.bash
```

### Launch RVIZ with config file

Note we use predefined config file but it is not necessary

```bash
(PC T2)$ rviz2 -d ~/dev_ws/src/manolobot_uno/config/bot_with_sensors.rviz
```

### Move the robot

#### With keyboard 

Launch keyboard teleop controller in PC:

```bash
(PC T3)$ ros2 run teleop_twist_keyboard teleop_twist_keyboard --ros-args -r /cmd_vel:=/diff_cont/cmd_vel_unstamped
```

Note remapping of topic `/cmd_vel` to `/diff_cont/cmd_vel_unstamped`

Now you can move the robot from computer with the keyboard and see it in RVIZ!

#### With a gamepad

More details in [./BOM/gamepad.md](./BOM/gamepad.md)

Connect the gamepad in Ubuntu:

* ensure it is charged (or charge with microUSB)
* to pair press HOME + SHARE (small button labelled 'S' on the left above the cross) until light flashes white (note if you press HOME + 'O' button on the right the white light blinks, not flashes)
* In Bluetooth settings select Wireless Controller to Connect. Light stops flashing and turns blue
* You may want to test it works with `$ evtest`

Launch gamepad controller:

```bash
$ ros2 launch manolobot_uno joystick.launch.py
```

Note: the controls are defined in a parameter file which implements:

- Dead man switches: L button (left shoulder) for normal speed, R button (right shoulder) for turbo
- Control on left stick: vertical axis for forward/backward motion and horizontal axis for rotation.

### Sensors

#### Stream camera

SSH to the robot from another Terminal and launch the camera controller:

```bash
(manubot T2)$ cd ~/dev_ws/
(manubot T2)$ source install/setup.bash
(manubot T2)$ ros2 launch manolobot_uno camera.launch.py
```

In RVIZ Add Camera and select topic `/image_raw/compressed`

It does not show the camera feed in RVIZ as it should... BUT it works with RQT:

```bash
(PC T4)$ cd ~/dev_ws/
(PC T4)$ source install/setup.bash 
(PC T4)$ ros2 run rqt_image_view rqt_image_view
```

It works!

#### Stream Lidar scans

Launch the LIDAR controller:

```bash
(manubot T3)$ cd ~/dev_ws/
(manubot T3)$ source install/setup.bash
(manubot T3)$ ros2 launch ldlidar_stl_ros2 ld06.launch.py 
```

It works!

## Power off manubot

Safe reset and shutdown: the blue button.

* Shortly pressing the Blue button is ignored (considered noise)
* ~1 sec press resets the RPi (not sure if there is a use case for this)
* 4 sec press shuts down safely the RPi

After Lidar powers off (means RPi powered off) switch off mains red button

See implementation in file `safe_shutdown.py` in: [](/home/mhered/manolobot/code/button/) 

## To Do

- [ ] add photos / video of battery charging
- [ ] fix issue with camera in RVIZ
- [ ] make power down more usable (remove short press for reset and provide feedback for shutdown)
- [ ] wheels skid, big time
- [ ] motors have a lot of hysteresis

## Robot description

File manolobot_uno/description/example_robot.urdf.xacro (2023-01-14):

<?xml version="1.0"?>
<robot xmlns:xacro="http://www.ros.org/wiki/xacro" name="robot">

    <material name="grey">
        <color rgba="0.2 0.2 0.2 1"/>
    </material>

    <material name="white">
        <color rgba="1 1 1 1"/>
    </material>

    <material name="orange">
        <color rgba="1 0.3 0.1 1"/>
    </material>

    <material name="blue">
        <color rgba="0 0 1 1"/>
    </material>


    <link name="world"></link>

    <joint name="world_to_base" type="fixed">
        <parent link="world" />
        <child link="base" />
        <origin rpy="1.57 0 0" xyz="0 0 0" />
    </joint>

    <link name="base">
        <visual>
            <origin xyz="2 0 0" rpy="0 0 0"/>
            <geometry>
                <box size="5 0.1 3" />
            </geometry>
            <material name="grey" />
        </visual>
    </link>


    <joint name="base_to_l3" type="revolute">
        <parent link="base" />
        <child link="l3" />
        <origin rpy="0 0 0" xyz="0 0.25 0" />
        <axis rpy="0 0 0" xyz="0 0 1" />
        <limit effort="0.1" lower="-3.1" upper="3.1" velocity="0.2"/>
    </joint>


    <link name="l3">
        <visual>
            <origin xyz="0.75 0 0" rpy="0 1.57 0"/>
            <geometry>
                <cylinder length="1.5" radius="0.04" />
            </geometry>
            <material name="orange" />
        </visual>
    </link>

    <joint name="l3_to_l2" type="revolute">
        <parent link="l3" />
        <child link="l2" />
        <!-- <origin xyz="1 0 0" /> -->
        <origin rpy="0 0 0" xyz="1.5 0 0" />
        <axis rpy="0 0 0" xyz="0 0 1" />
        <limit effort="0.1" lower="-3.1" upper="3.1" velocity="0.2"/>
    </joint>


    <link name="l2">
        <visual>
            <origin xyz="0.75 0 0" rpy="0 1.57 0"/>
            <geometry>
                
                <cylinder length="1.5" radius="0.04" />
            </geometry>
            <material name="orange" />
        </visual>
    </link>

    <joint name="l2_to_l1" type="revolute">
        <parent link="l2" />
        <child link="l1" />
        <origin rpy="0 0 0" xyz="1.5 0 0" />
        <axis rpy="0 0 0" xyz="0 0 1" />
        <limit effort="0.1" lower="-3.1" upper="3.1" velocity="0.2"/>
    </joint>


    <link name="l1">
        <visual>
            <origin xyz="0.5 0 0" rpy="0 1.57 0"/>
            <geometry>
                
                <cylinder length="1" radius="0.04" />
            </geometry>
            <material name="orange" />
        </visual>
    </link>


    <joint name="l1_to_grip" type="revolute">
        <parent link="l1" />
        <child link="grip" />
        <origin rpy="0 0 0" xyz="1 0 0" />
        <axis rpy="0 0 0" xyz="0 0 1" />
        <limit effort="0.1" lower="-3.1" upper="3.1" velocity="0.2"/>
    </joint>


    <link name="grip">
        <visual>
            <origin xyz="0.25 0 0"/>
            <geometry>
                <box size="0.5 0.5 0.05" />
            </geometry>
            <material name="white" />
        </visual>
    </link>



    <joint name="world_to_camera" type="fixed">
        <parent link="world" />
        <child link="camera" />
        <origin rpy="-2 0 2.5" xyz="4 1 2" />
    </joint>

    <link name="camera">
        <visual>
            <origin xyz="0 0 -0.2"/>
            <geometry>
                <box size="0.2 0.2 0.4" />
            </geometry>
            <material name="blue" />
        </visual>
    </link>


</robot>

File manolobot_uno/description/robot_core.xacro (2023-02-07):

<?xml version="1.0"?>
<robot xmlns:xacro="http://www.ros.org/wiki/xacro" >

    <!-- MATERIALS -->
    <!-- white black light_gray dark_gray green blue red yellow orange -->

    <xacro:include filename="materials.xacro" />

    <!-- INERTIAL MACROS -->

    <xacro:include filename="inertial_macros.xacro" />

    <!-- BASE LINK -->  
  
    <link name="base_link">
    </link>

    <!-- CHASSIS LINK --> 

    <joint name="chassis_joint" type = "fixed">
        <parent link="base_link" />
        <child link="chassis_link" />
        <origin xyz="${W_x-box_x/2} 0 ${W_z}" />
    </joint>
    
    <link name="chassis_link">
        <visual>
            <geometry>
                <box size="${box_x} ${box_y} ${box_z}"/>
            </geometry>
            <origin xyz="${box_x/2} 0 ${box_z/2}" />
            <material name="white" />
        </visual>

        <collision>
            <geometry>
                <box size="${box_x} ${box_y} ${box_z}"/>
            </geometry>
            <origin xyz="${box_x/2} 0 ${box_z/2}" />
        </collision>

        <xacro:inertial_box mass="${box_mass}" x="${box_x}" y="${box_y}" z="${box_z}">
            <origin xyz="${box_x/2} 0 ${box_z/2}" rpy="0 0 0" />
        </xacro:inertial_box>

    </link>

    <gazebo reference="chassis_link">
        <material>Gazebo/White</material>
    </gazebo>

    <!-- LEFT WHEEL LINK --> 

    <joint name="left_wheel_joint" type = "continuous">
        <parent link="base_link" />
        <child link="left_wheel_link" />
        <origin xyz="0 ${W_y} 0" rpy="-${pi/2} 0 0" />
        <axis xyz="0 0 1" />
    </joint>
    
    <link name="left_wheel_link">
        <visual>
            <geometry>
                <cylinder radius="${W_D/2}" length="${W_h}" />
            </geometry>
            <material name="blue" />
        </visual>

        <collision>
            <geometry>
                <sphere radius="${W_D/2}" />
            </geometry>
        </collision>

        <xacro:inertial_cylinder mass="${W_mass}" radius="${W_D/2}" length="${W_h}">
            <origin xyz="0 0 0" rpy="0 0 0" />
        </xacro:inertial_cylinder>

    </link>

    <gazebo reference="left_wheel_link">
        <material>Gazebo/Blue</material>
    </gazebo>

    <!-- RIGHT WHEEL LINK --> 

    <joint name="right_wheel_joint" type = "continuous">
        <parent link="base_link" />
        <child link="right_wheel_link" />
        <origin xyz="0 -${W_y} 0" rpy="${pi/2} 0 0" />
        <axis xyz="0 0 -1" />
    </joint>
    
    <link name="right_wheel_link">
        <visual>
            <geometry>
                <cylinder radius="${W_D/2}" length="${W_h}" />
            </geometry>
            <material name="blue" />
        </visual>

        <collision>
            <geometry>
                <sphere radius="${W_D/2}" />
            </geometry>
        </collision> 

        <xacro:inertial_cylinder mass="${W_mass}" radius="${W_D/2}" length="${W_h}">
            <origin xyz="0 0 0" rpy="0 0 0" />
        </xacro:inertial_cylinder>

    </link>

    <gazebo reference="right_wheel_link">
        <material>Gazebo/Blue</material>
    </gazebo>

<!-- LEFT CASTER WHEEL LINK -->

    <joint name="left_caster_wheel_joint" type = "fixed">
        <parent link="chassis_link" />
        <child link="left_caster_wheel_link" />
        <origin xyz="${box_x-c_x} ${box_y/2-c_y} ${-c_z}" />
    </joint>
    
    <link name="left_caster_wheel_link">
        <visual>
            <geometry>
                <sphere radius="${c_D/2}" />
            </geometry>
            <material name="yellow" />
        </visual>

        <collision>
            <geometry>
                <sphere radius="${c_D/2}" />
            </geometry>
        </collision>
        
        <xacro:inertial_sphere mass="${c_mass}" radius="${c_D/2}">
            <origin xyz="0 0 0" rpy="0 0 0" />
        </xacro:inertial_sphere>

    </link>

    <gazebo reference="left_caster_wheel_link">
        <material>Gazebo/Yellow</material>
        <mu1 value="0.0001" />
        <mu2 value="0.0001" />
    </gazebo>



<!-- RIGHT CASTER WHEEL LINK     -->

    <joint name="right_caster_wheel_joint" type = "fixed">
        <parent link="chassis_link" />
        <child link="right_caster_wheel_link" />
        <origin xyz="${box_x-c_x} ${-box_y/2+c_y} ${-c_z}" />
    </joint>
    
    <link name="right_caster_wheel_link">
        <visual>
            <geometry>
                <sphere radius="${c_D/2}" />
            </geometry>
            <material name="yellow" />
        </visual>
        
        <collision>
            <geometry>
                <sphere radius="${c_D/2}" />
            </geometry>
        </collision>
        
        <xacro:inertial_sphere mass="${c_mass}" radius="${c_D/2}">
            <origin xyz="0 0 0" rpy="0 0 0" />
        </xacro:inertial_sphere>
                
    </link>

    <gazebo reference="right_caster_wheel_link">
        <material>Gazebo/Yellow</material>
        <mu1 value="0.0001" />
        <mu2 value="0.0001" />
    </gazebo>



    <!-- LEFT MOTOR LINK --> 

    <joint name="left_motor_joint" type = "fixed">
        <parent link="base_link" />
        <child link="left_motor_link" />
        <origin xyz="0 ${m_y+m_h/2} 0" rpy="-${pi/2} 0 0" />
    </joint>
    
    <link name="left_motor_link">
        <visual>
            <geometry>
                <cylinder radius="${m_D/2}" length="${m_h}" />
            </geometry>
            <origin xyz="0 0 0" />
            <material name="red" />
        </visual>

        <visual>
            <geometry>
                <cylinder radius="${m_d/2}" length="${m_l}" />
            </geometry>
            <origin xyz="0 0 ${(m_h+m_l)/2}" />
            <material name="red" />
        </visual>

        <collision>
            <geometry>
                <cylinder radius="${m_D/2}" length="${m_h}" />
            </geometry>
        </collision>

        <xacro:inertial_cylinder mass="${m_mass}" radius="${m_D/2}" length="${m_h}">
            <origin xyz="0 0 0" rpy="0 0 0" />
        </xacro:inertial_cylinder>

    </link>

    <gazebo reference="left_motor_link">
        <material>Gazebo/Red</material>
    </gazebo>


    <!-- RIGHT MOTOR LINK --> 

    <joint name="right_motor_joint" type = "fixed">
        <parent link="base_link" />
        <child link="right_motor_link" />
        <origin xyz="0 -${m_y+m_h/2} 0" rpy="${pi/2} 0 0" />
    </joint>
    
    <link name="right_motor_link">
        <visual>
            <geometry>
                <cylinder radius="${m_D/2}" length="${m_h}" />
            </geometry>
            <origin xyz="0 0 0" />
            <material name="red" />
        </visual>

        <visual>
            <geometry>
                <cylinder radius="${m_d/2}" length="${m_l}" />
            </geometry>
            <origin xyz="0 0 ${(m_h+m_l)/2}" />
            <material name="red" />
        </visual>

        <collision>
            <geometry>
                <cylinder radius="${m_D/2}" length="${m_h}" />
            </geometry>
        </collision>

        <xacro:inertial_cylinder mass="${m_mass}" radius="${m_D/2}" length="${m_h}">
            <origin xyz="0 0 0" rpy="0 0 0" />
        </xacro:inertial_cylinder>

    </link>

    <gazebo reference="right_motor_link">
        <material>Gazebo/Red</material>
    </gazebo>

</robot>

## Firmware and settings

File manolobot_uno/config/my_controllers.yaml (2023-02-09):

controller_manager:
  ros__parameters:
    update_rate: 30
    # use_sim_time: true

    diff_cont:
      type: diff_drive_controller/DiffDriveController

    joint_broad:
      type: joint_state_broadcaster/JointStateBroadcaster


diff_cont:
  ros__parameters:

    publish_rate: 30.0

    base_frame_id: base_link

    left_wheel_names: ['left_wheel_joint']
    right_wheel_names: ['right_wheel_joint']
    wheel_separation: 0.244
    wheel_radius: 0.0325

    # <xacro:property name="W_y" value="0.122"/> <!-- wheel half separation -->
    # <xacro:property name="W_D" value="0.065"/> <!-- wheel diameter -->

    use_stamped_vel: false

    # open_loop: false    

    # wheels_per_side: x
    # wheel_separation_multiplier: x
    # left_wheel_radius_multiplier: x
    # right_wheel_radius_multiplier: x

    # odom_frame_id: x
    # pose_covariance_diagonal: x
    # twist_covariance_diagonal: x
    # open_loop: x
    # enable_odom_tf: x

    # cmd_vel_timeout: x
    # publish_limited_velocity: x
    # velocity_rolling_window_size: x
    

    # linear.x.has_velocity_limits: false
    # linear.x.has_acceleration_limits: false
    # linear.x.has_jerk_limits: false
    # linear.x.max_velocity: NAN
    # linear.x.min_velocity: NAN
    # linear.x.max_acceleration: NAN
    # linear.x.min_acceleration: NAN
    # linear.x.max_jerk: NAN
    # linear.x.min_jerk: NAN

    # angular.z.has_velocity_limits: false
    # angular.z.has_acceleration_limits: false
    # angular.z.has_jerk_limits: false
    # angular.z.max_velocity: NAN
    # angular.z.min_velocity: NAN
    # angular.z.max_acceleration: NAN
    # angular.z.min_acceleration: NAN
    # angular.z.max_jerk: NAN
    # angular.z.min_jerk: NAN


# joint_broad:
#   ros__parameters:

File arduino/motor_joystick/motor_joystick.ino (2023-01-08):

// Motor A connections
int enA = 9;
int in1 = 8;
int in2 = 7;

// Motor B connections
int enB = 3;
int in3 = 5;
int in4 = 4;

// Joystick connections
const int pinJoyX = A0;
const int pinJoyY = A1;


void setup() {
  
  Serial.begin(9600);
  // Set all the motor control pins to outputs
  pinMode(enA, OUTPUT);
  pinMode(enB, OUTPUT);
  pinMode(in1, OUTPUT);
  pinMode(in2, OUTPUT);
  pinMode(in3, OUTPUT);
  pinMode(in4, OUTPUT);
  
  // Turn off motors - Initial state
  digitalWrite(in1, LOW);
  digitalWrite(in2, LOW);
  digitalWrite(in3, LOW);
  digitalWrite(in4, LOW);
}

void loop() {

   int Xvalue = 0;
   int Yvalue = 0;

   //read values
   Xvalue = analogRead(pinJoyX);
   delay(100);   // short delay needed between analog readings
   Yvalue = analogRead(pinJoyY);

   //compute motorA, motorB and fwdA, fwdB from analog input Xvalue, Yvalue
   bool fwdA = true;
   bool fwdB = true;
   int motorA = map(Yvalue,0,1023,255,-255) + map(Xvalue,0,1023,-255,255);
   int motorB = map(Yvalue,0,1023,255,-255) - map(Xvalue,0,1023,-255,255);
      
   if (motorA < 0) 
   {
      fwdA = false;
      motorA = - motorA;
   }

   if (motorB < 0) 
   {
      fwdB = false;
      motorB = - motorB;
   }

   if (motorA>255) motorA=255;
   if (motorB>255) motorB=255;

  // avoid humming
  if (motorA<15) motorA = 0;
  if (motorB<15) motorB = 0;
  

   //show values through serial
   Serial.print("(X, Y): (");
   Serial.print(Xvalue);
   Serial.print(", ");
   Serial.print(Yvalue);
   Serial.print(") | motorA: ");
   if (fwdA == false) {
    Serial.print("-");
   }
   Serial.print(map(motorA, 0,255,0,100));
   Serial.print("% | motorB: ");
   if (fwdB == false) {
    Serial.print("-");
   } 
   Serial.print(map(motorB,0,255,0,100));   
   Serial.println("%");      
   // operate motors

  if (fwdA == true)
  {
    // move motor A forward
    digitalWrite(in1, HIGH);
    digitalWrite(in2, LOW);
  } 
  else {
    // move motor A in reverse
    digitalWrite(in1, LOW);
    digitalWrite(in2, HIGH);
  }

  if (fwdB == true)
  {
    // move motor B forward
    digitalWrite(in3, HIGH);
    digitalWrite(in4, LOW);
  } 
  else {
    // move motor B in reverse
    digitalWrite(in3, LOW);
    digitalWrite(in4, HIGH);
  }
  
   analogWrite(enA, motorA);
   analogWrite(enB, motorB);
   
   delay(100);
}

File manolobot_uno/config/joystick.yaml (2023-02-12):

# Parameter file for joystick

joy_node:
  ros__parameters:
    device_id: 0
    deadzone: 0.05
    autorepeat_rate: 20.0

teleop_node:
  ros__parameters:
    axis_linear:  
      x: 1      # Left thumb stick vertical
    scale_linear: 
      x: 0.5    # regular speed 0.5 m/s
    scale_linear_turbo:
      x: 1.0    # turbo speed 1 m/s

    axis_angular:  
      yaw: 0    # Left thumb stick horizontal
    scale_angular: 
      yaw: 1.0  # regular speed 1 rad/s
    scale_angular_turbo: 
      yaw: 2.0  # turbo speed 2 rad/s

    require_enable_button: true
    enable_button: 4  # Left shoulder button: dead man switch for regular speed
    enable_turbo_button: 5  # Right shoulder button: dead man switch for turbo speed

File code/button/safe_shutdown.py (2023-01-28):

# Based on code written by Ho Yun "Bobby" Chan @ SparkFun Electronics
# and released under the MIT License (http://opensource.org/licenses/MIT)
#
#        https://learn.sparkfun.com/tutorials/raspberry-pi-safe-reboot-and-shutdown-button/

# Tutorial to adjust the "rc.local" file and run at startup:
#
#        https://learn.sparkfun.com/tutorials/raspberry-pi-safe-reboot-and-shutdown-button
#

import time
import RPi.GPIO as GPIO

# Pin definition
shutdown_pin = 17

# Suppress warnings
GPIO.setwarnings(False)

# Use "GPIO" pin numbering
GPIO.setmode(GPIO.BCM)

# Use built-in internal pullup resistor so the pin is not floating
# if using a momentary push button without a resistor.
GPIO.setup(shutdown_pin, GPIO.IN, pull_up_down=GPIO.PUD_UP)

# modular function to shutdown Pi
def shut_down():
    print("Shutting down")
    command = "/usr/bin/sudo /sbin/shutdown -h now"
    import subprocess
    process = subprocess.Popen(command.split(), stdout=subprocess.PIPE)
    output = process.communicate()[0]
    print(output)

# modular function to shutdown Pi
def reboot():
    print("Rebooting")
    command = "/usr/bin/sudo /sbin/shutdown -r now"
    import subprocess
    process = subprocess.Popen(command.split(), stdout=subprocess.PIPE)
    output = process.communicate()[0]
    print(output)

def press_button():
    start_time=time.time()
    time_pressed=0
    noise_time=1
    hold_time=4

    while GPIO.input(shutdown_pin) == False and (time_pressed < hold_time) :
        time_pressed=time.time()-start_time

    if time_pressed < noise_time:
        print("Ignoring short button press")
    elif noise_time < time_pressed < hold_time:
        print("Detected a short button press: Rebooting the RPi")
        reboot()
    else:
        print("Detected a long button press: Shutting down the RPi")
        shut_down()
    

# Main loop
while True:
    #short delay, otherwise this code will take up a lot of the Pi's processing power
    time.sleep(0.5)

    # uncomment for troubleshooting: 
    # print('GPIO state is = ', GPIO.input(shutdown_pin))
    if GPIO.input(shutdown_pin) == False:
        press_button()

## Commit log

2022-11-22 Touchscreen setup and Lidar description
2022-11-27 Add Pi camera
2022-12-04 Prototype status and todo
2022-12-29 Make /BOM/ folder. Add status on 28.12, images.
2023-01-04 Control motors with a joystick
2023-01-04 Program the Arduino from the laptop through RPi
2023-01-05 Use Arduino map() function to re-scale ranges. Print motor power in %.
2023-01-07 Cut power to motors below a threshold to avoid humming
    [motor_joystick.ino]
2023-01-07 Add storage box to BOM
2023-01-07 Remap Yvalue to 255, -255
    Remap Yvalue so that wheels rotate in the proper direction after
    they were mounted in the chassis:
    * motorA operates LH wheel
    * motorB operates RH wheel
    * RED, WHITE cables rewired:
    - motorA RED -> OUT1
    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
2023-01-08 Description of chassis
2023-01-08 Move images of BOM files to ./BOM/assets/images/
2023-01-08 Update of prototype status 7/1/23 incl pics
2023-01-10 Notes on describing the robot in URDF
2023-01-13 Links to 3D printed parts
2023-01-14 Move manolobot_uno inside main repo
    [example_robot.urdf.xacro, inertial_macros.xacro, materials.xacro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]
2023-01-14 Rename URDF.md to Part-4 and link it from README.md
2023-01-14 Move notes on TF and URDF prerequisites to Part-1
2023-01-15 Prepare for Gazebo visualization
    * launch_sim.launch.py: new launch file to launch gazebo and spawn robot
    with a single command
    * robot.urdf.xacro: add call to properties.xacro and gazebo_control.xacro
    * robot_core.xacro:
    - move properties definition (robot dimensions etc) to a separate file
    - add gazebo tags to define colors for each link
    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
    [gazebo_control.xacro, properties.xacro, robot.urdf.xacro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]
2023-01-15 Adjust masses to improve behaviour - values are not real though
    [properties.xacro]
2023-01-17 Battery and charger
2023-01-18 Add Lidar to robot model
    * description/lidar.xacro: new file to define Lidar properties
    * description/properties.xacro: rename box dimensions from L_x L_y L_z
    to box_x box_y box_z and leave L_ prefix for lidar
    * description/robot_core.xacro and robot.urdf.xacro: modify accordingly
    * worlds/cones.world: a sample world with cones
    [lidar.xacro, properties.xacro, robot.urdf.xacro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]
2023-01-20 Add camera to robot model
    * description/camera.xacro: new file to define camera properties
    * description/properties.xacro: add camera properties with cam_
    prefix
    * description/robot.urdf.xacro: include camera.xacro
    * description/robot_core.xacro: change color of caster wheel
    * BOM/pi_camera.md: Add notes on cameras in ROS
    * config/bot_with_sensors.rviz: RVIZ config file for robot with
    sensors
    * worlds/cones.world: recreated to fix issue
    This setup was used to record the video gazebo2.mp4. The robot
    - operated with the gamepad - drives around a field of cones and
    shows output of camera and lidar.
    [camera.xacro, properties.xacro, robot.urdf.xacro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]
2023-01-21 Set up robot camera and add selfie.
2023-01-21 Add launch file for camera
2023-01-21 Update FOV to value of Pi Camera
    [camera.xacro]
2023-01-21 Configure lidar on bot
2023-01-23 Add 3D printed parts
    [lidar.stl, micro_Apex_gopro.stl, picam_A.STL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]
2023-01-23 Clarify battery charging rate
2023-01-28 Script for safe reboot/shutdown button
    [safe_shutdown.py]
2023-01-28 Instructions to implement safe reset/shutdown button
2023-01-31 Move arduino code to ./code/arduino
2023-01-31 Replaced symlink for actual contents of ./code/arduino/ROSArduinoBridge
    [ROSArduinoBridge.ino]
2023-01-31 Control motors from PC, with wiring diagram. Lower resolution of all diagrams.
2023-02-01 Wiring diagram with encoders
2023-02-01 Revert AUTO_STOP_INTERVAL to default value of 2sec
    [ROSArduinoBridge.ino]
2023-02-02 First attempt at switching off the LiDAR - not working
2023-02-02 Calibration and 1st steps at teleoperation
2023-02-05 Teleoperation with ros2_control and teleop_twist_keyboard
    [my_controllers.yaml, robot.urdf.xacro, ros2_control.xacro]
2023-02-07 Spheres as collision for wheels to reduce drift in gazebo
    [robot_core.xacro]
2023-02-07 Add parameter to toggle between gazebo_control and ros2_control
    [robot.urdf.xacro]
2023-02-09 Implement teleoperation in real robot
    [my_controllers.yaml, ros2_control.xacro]
2023-02-11 Device address by-id
    [ros2_control.xacro]
2023-02-11 Reduce image to 320x240 and set frame rate to 30Hz
2023-02-11 Configure rviz2 for real robot with sensors
2023-03-09 First CAD model
    [bot_1-Base_Groove.stl, bot_1-Cap.stl, bot_1.FCStd]
2023-03-10 bot_2 design at 1:1 scale
    [bot_2-Base_Groove.stl, bot_2-Cap.stl, bot_2.FCStd]
2023-10-19 Improve section on charging the battery
2023-10-28 Notes on Docker videos part 2 & 3 and sample files in /docker folder
2023-12-15 Devices in docker: gamepad and camera
2025-01-07 Add notes on command for Arduino libraries
2025-01-07 Clean up of CAD folder
    * New .gitignore to exclude folders:
    - STL: contains STL exports for 3D printing)
    - downloaded: CAD files of COTS components downloaded from public repositories
    * Add CAD models of the bot v3 and v4
    * clean temp files
    [bot_1-Base_Groove.stl, bot_1-Cap.stl, bot_2-Base_Groove.stl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]
